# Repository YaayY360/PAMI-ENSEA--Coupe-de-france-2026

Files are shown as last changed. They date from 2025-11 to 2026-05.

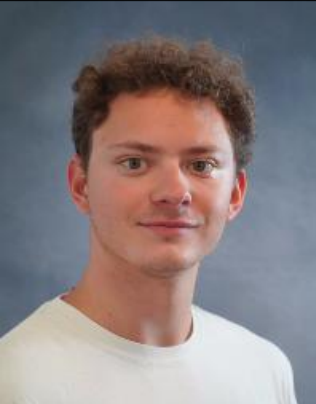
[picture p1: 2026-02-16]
Diagramme-architecture/Photo-collaborateurs/Yanis.png

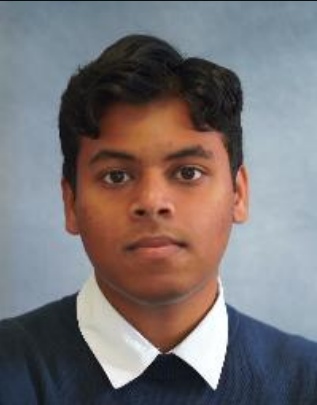
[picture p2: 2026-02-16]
Diagramme-architecture/Photo-collaborateurs/Valentin.png

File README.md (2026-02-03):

# 🔧 Coupe de france de robotique 2026 - PAMI ENSEA 

> **Objectif :** Conception et fabrication d'un robot PAMI (Petit Actionneur Motorisé Indépendant) respectant les modalités attendues pour la coupe de france de robotique 2026.
> 
> **Membres de l'équipe :**
> 
> CHERFI Iftene (1G1)
> 
> EL BAROUD Elias (1G1)
> 
> GRAVE Yanis (1G1)
> 
> LINOT Jean-Bosco (1G1)
> 
> MALEPART Alexandre (1G3)
>
> NEJJARI Mouaad (1G3)
>
> SURESHKUMAR Valentin (1G1)
---

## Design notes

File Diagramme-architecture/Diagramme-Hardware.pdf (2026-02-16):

# Diagramme d’architecture Hardware

Composant d’Alimentation | Composant Actif Microcontrôleur | Composant Passif Batterie 7.5

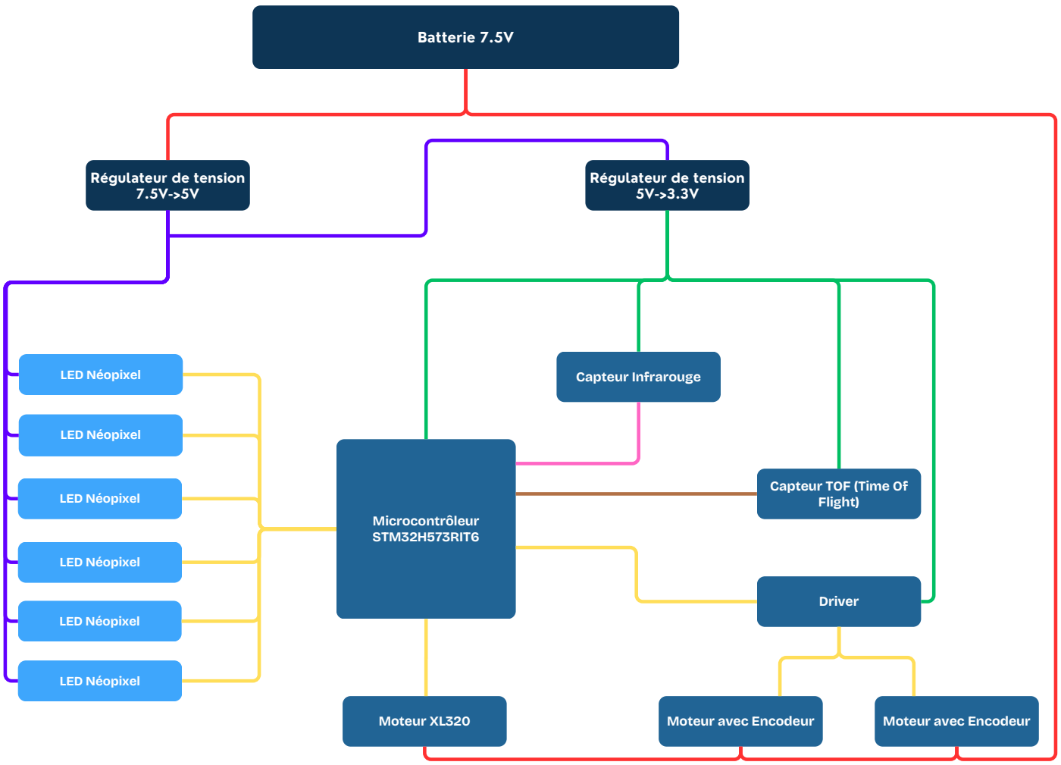
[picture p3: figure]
Régulateur de tension 7.5V->5V; Régulateur de tension 5V->3.3V; Batterie 7.5V; LED Néopixel; Capteur Infrarouge; Microcontrôleur STM32H573RIT6; Capteur TOF (Time Of Flight); Driver; Moteur XL320; Moteur avec Encodeur

| STM32H573RIT6 | LED Néopixel

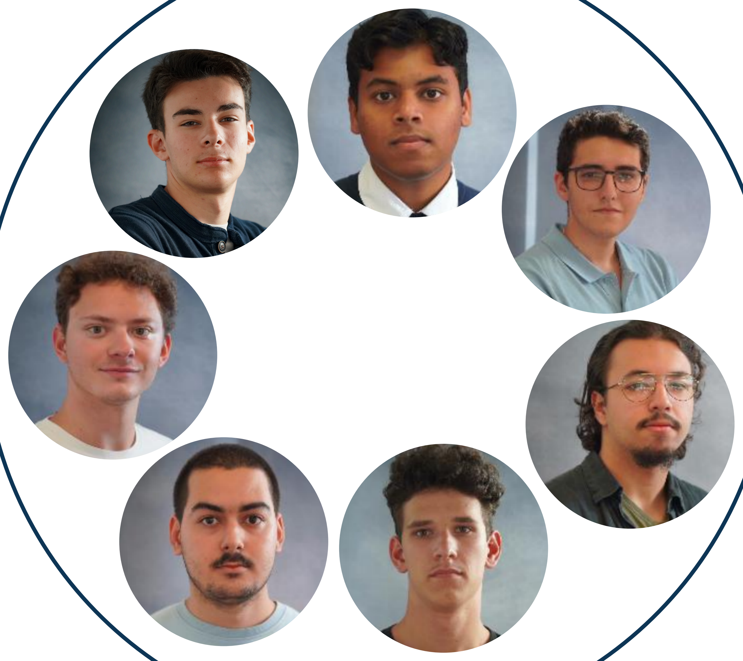
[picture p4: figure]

Régulateur de tension 7.5->5V | Capteur Infrarouge
Régulateur de tension 5->3.3V | Capteur TOF (Time Of Flight)
| Driver
| Moteur avec Encodeur
| Moteur XL320

# Colaborate

7.5V

3.3V

5V

PWM

SPI

I2C

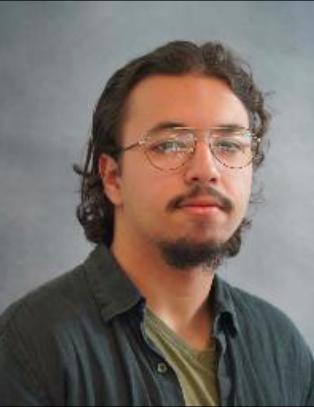
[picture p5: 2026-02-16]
Diagramme-architecture/Photo-collaborateurs/Elias.png

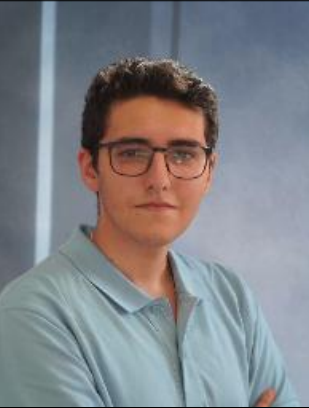
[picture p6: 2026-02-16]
Diagramme-architecture/Photo-collaborateurs/Iftene.png

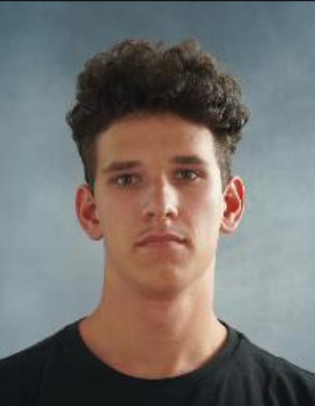
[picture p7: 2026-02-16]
Diagramme-architecture/Photo-collaborateurs/Jean.png

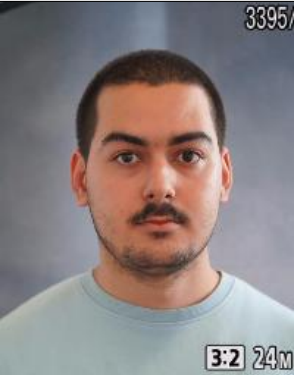
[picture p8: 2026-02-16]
Diagramme-architecture/Photo-collaborateurs/Mouaad.png

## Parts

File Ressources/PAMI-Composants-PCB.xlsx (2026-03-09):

Connecteur 01x06 pour | Référence | site fabriquant | quantité
Microcontroleur | STM32H573RIT6 |  | 1
STLINK | STLINKV3MOD |  | 1
Régulateur 3.3V | AZ1117CH2 - 3.3 |  | 1
Régulateur 5.0V | wurth elektronik DC-DC 5.0V | https://www.mouser.fr/ProductDetail/Wurth-Elektronik/173010578?qs=%252BUQ4csG8RsfFs4nK53SHEg%3D%3D | 1
Connecteurs pour 2 moteur odométriques | conn jst xh 01x06 |  | 3
Connecteur pour TOF | (horizontal) pin_header 01x06
Connecteurs
Connecteurs
Drivers pour 2 moteur odométriques | TB6612FNG |  | 1
Moteurs pour roues | Moteur CC N20-1812-EN |  | 2
Moteur pour animation | XL320 |  | 1
Led néo pixels | WS2812B RGB LED chip | https://mmwork.shop/boutique/led-adressable-ws2812b-rgb-5050-smd/
Boutons |  |  | 4
Led alim | LED CMS |  | 1
condensateur 1 MicroFarad | WCAP-CSGP Ceramic Capacitors 0603 | https://www.we-online.com/components/products/datasheet/885012206076.pdf
Capteur TOF | VL53T0

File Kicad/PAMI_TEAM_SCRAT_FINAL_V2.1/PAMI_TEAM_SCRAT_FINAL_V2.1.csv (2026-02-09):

Reference | Qty | Value | DNP | Exclude from BOM | Exclude from Board | Footprint | Datasheet
C1,C2,C3 | 3 | 10n |  |  |  | Capacitor_SMD:C_0603_1608Metric | ~
C4,C5,C6,C7,C8,C9,C10,C15,C17 | 9 | 100n |  |  |  | Capacitor_SMD:C_0603_1608Metric | ~
C11,C16,C18 | 3 | 10u |  |  |  | Capacitor_SMD:C_0603_1608Metric | ~
C12 | 1 | 22u |  |  |  | Capacitor_SMD:C_Elec_5x5.4 | ~
C13,C14 | 2 | 20p |  |  |  | Capacitor_SMD:C_0603_1608Metric | ~
C19,C20 | 2 | 22u |  |  |  | Capacitor_SMD:C_0603_1608Metric | ~
C21,C22,C23,C24,C25 | 5 | 1u |  |  |  | Capacitor_SMD:C_0603_1608Metric | ~
D1 | 1 | LED |  |  |  | LED_SMD:LED_0603_1608Metric | ~
D2,D3,D4,D5,D6,D7 | 6 | NeoPixel |  |  |  | LED_SMD:LED_WS2812B_PLCC4_5.0x5.0mm_P3.2mm | https://www.adafruit.com/product/1938
H1,H2,H3,H4 | 4 | MountingHole_Pad |  | Exclure de la Liste du Matériel |  | MountingHole:MountingHole_3.2mm_M3_DIN965_Pad | ~
J1 | 1 | ALIM |  |  |  | Connector_JST:JST_XH_B2B-XH-A_1x02_P2.50mm_Vertical | ~
J2 | 1 | TOF |  |  |  | Connector_PinSocket_2.54mm:PinSocket_1x06_P2.54mm_Horizontal | ~
J3 | 1 | IR |  |  |  | Connector_JST:JST_XH_B6B-XH-A_1x06_P2.50mm_Vertical | ~
J4 | 1 | M1 |  |  |  | Connector_JST:JST_XH_B6B-XH-A_1x06_P2.50mm_Vertical | ~
J5 | 1 | M2 |  |  |  | Connector_JST:JST_XH_B6B-XH-A_1x06_P2.50mm_Vertical | ~
J6 | 1 | XL320 |  |  |  | Connector_JST:JST_XH_B3B-XH-A_1x03_P2.50mm_Vertical | ~
R1,R2,R3,R4,R5,R6,R7 | 7 | 10k |  |  |  | Resistor_SMD:R_0603_1608Metric | ~
R8,R9 | 2 | 510 |  |  |  | Resistor_SMD:R_0603_1608Metric | ~
SW1 | 1 | BTN1 |  |  |  | Button_Switch_SMD:Panasonic_EVQPUJ_EVQPUA | ~
SW2 | 1 | BTN2 |  |  |  | Button_Switch_SMD:Panasonic_EVQPUJ_EVQPUA | ~
SW3 | 1 | BTN3 |  |  |  | Button_Switch_SMD:Panasonic_EVQPUJ_EVQPUA | ~
SW4 | 1 | RESET |  |  |  | Button_Switch_SMD:Panasonic_EVQPUJ_EVQPUA | ~
U1 | 1 | STM32H573RITx |  |  |  | Package_QFP:LQFP-64_10x10mm_P0.5mm | https://www.st.com/resource/en/datasheet/stm32h573ri.pdf
U2 | 1 | STLINK-V3MODS |  |  |  | STLINK-V3MODS:MODULE_STLINK-V3MODS
U3 | 1 | WE-DC-DC-5V |  |  |  | Converter_DCDC:Converter_DCDC_RECOM_R-78B-2.0_THT | https://www.diodes.com/assets/Datasheets/AZ1117C.pdf
U4 | 1 | AZ1117CH2-3.3 |  |  |  | Package_TO_SOT_SMD:SOT-223-3_TabPin2 | https://www.diodes.com/assets/Datasheets/AZ1117C.pdf
U5 | 1 | TB6612FNG |  |  |  | Package_SO:SSOP-24_5.3x8.2mm_P0.65mm | https://toshiba.semicon-storage.com/us/product/linear/motordriver/detail.TB6612FNG.html
Y1 | 1 | Crystal |  |  |  | Crystal:Crystal_SMD_7050-4Pin_7.0x5.0mm | ~

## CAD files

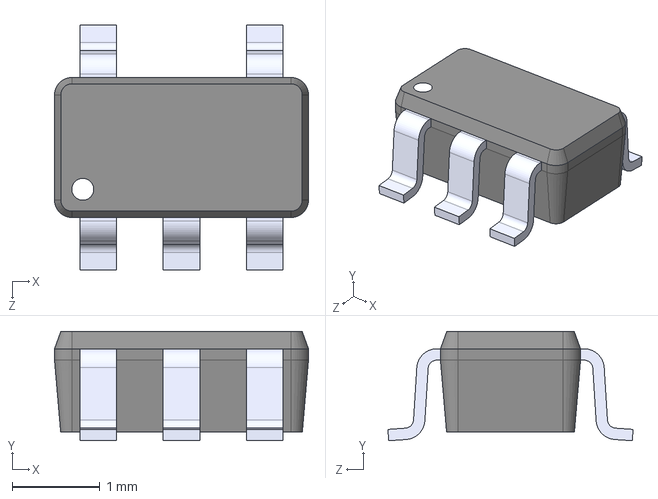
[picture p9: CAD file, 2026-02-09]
Kicad/Librairies KICAD/BU33SD5WG-TR/BU33SD5WG-TR.step
2.90 x 1.25 x 2.80 mm

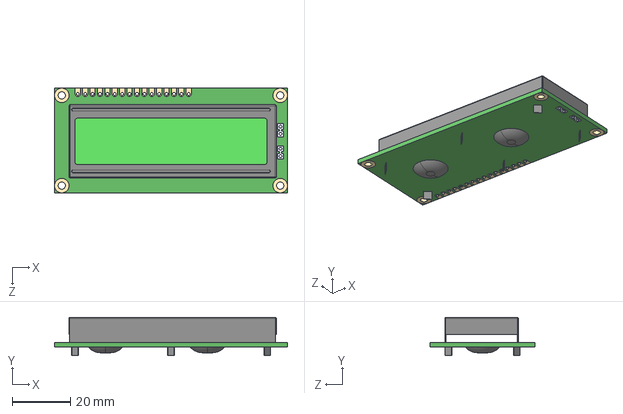
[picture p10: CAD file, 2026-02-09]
Kicad/Librairies KICAD/LCD-16X2/LCD-16X2.step
80.0 x 13.2 x 36.0 mm

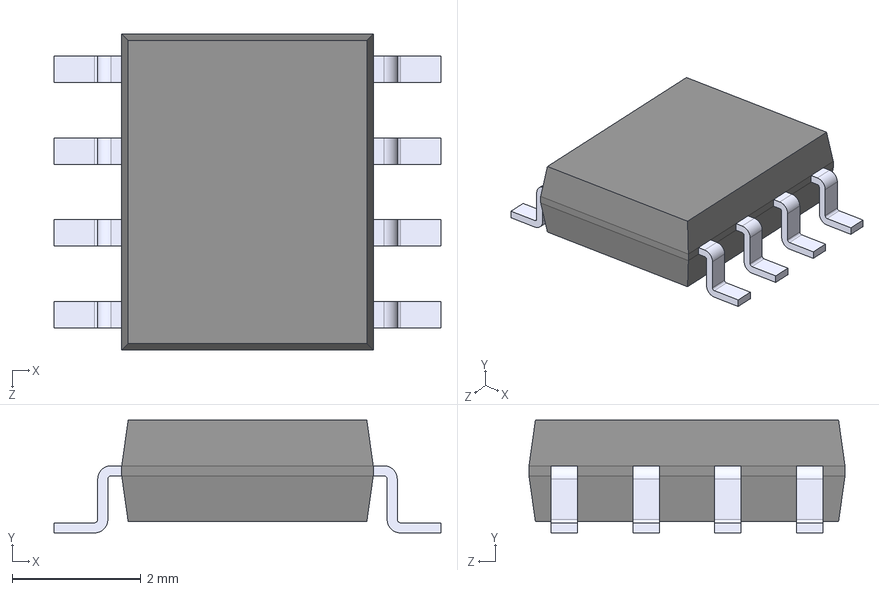
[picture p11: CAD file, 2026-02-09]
Kicad/Librairies KICAD/MCP4801-E_SN/MCP4801-E_SN.step
6.00 x 1.75 x 4.90 mm

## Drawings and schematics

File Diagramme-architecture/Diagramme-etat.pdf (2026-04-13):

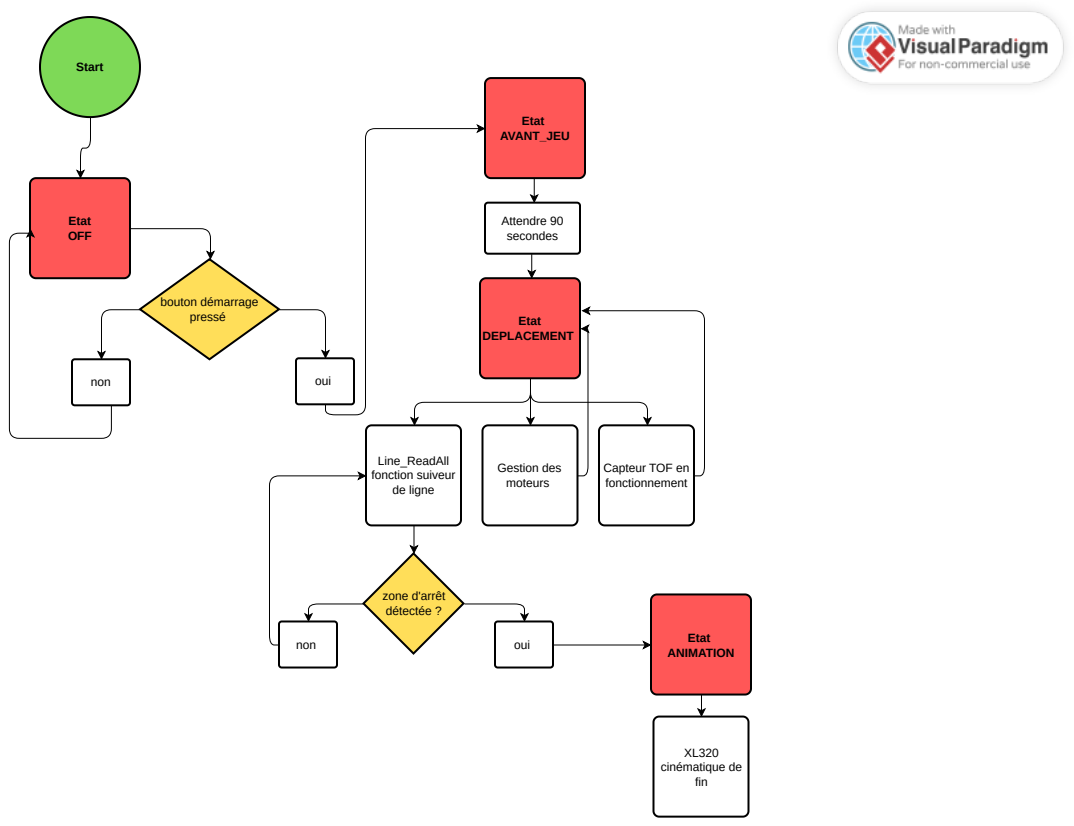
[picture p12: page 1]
Start; Etat OFF; oui; Etat AVANT_JEU; Line_ReadAll fonction suiveur de ligne; bouton démarrage pressé; non; Attendre 90 secondes; Etat DEPLACEMENT; Gestion des moteurs; zone d'arrêt détectée ?; Etat; ANIMATION; XL320 cinématique de fin

Capteur TOF en
fonctionnement

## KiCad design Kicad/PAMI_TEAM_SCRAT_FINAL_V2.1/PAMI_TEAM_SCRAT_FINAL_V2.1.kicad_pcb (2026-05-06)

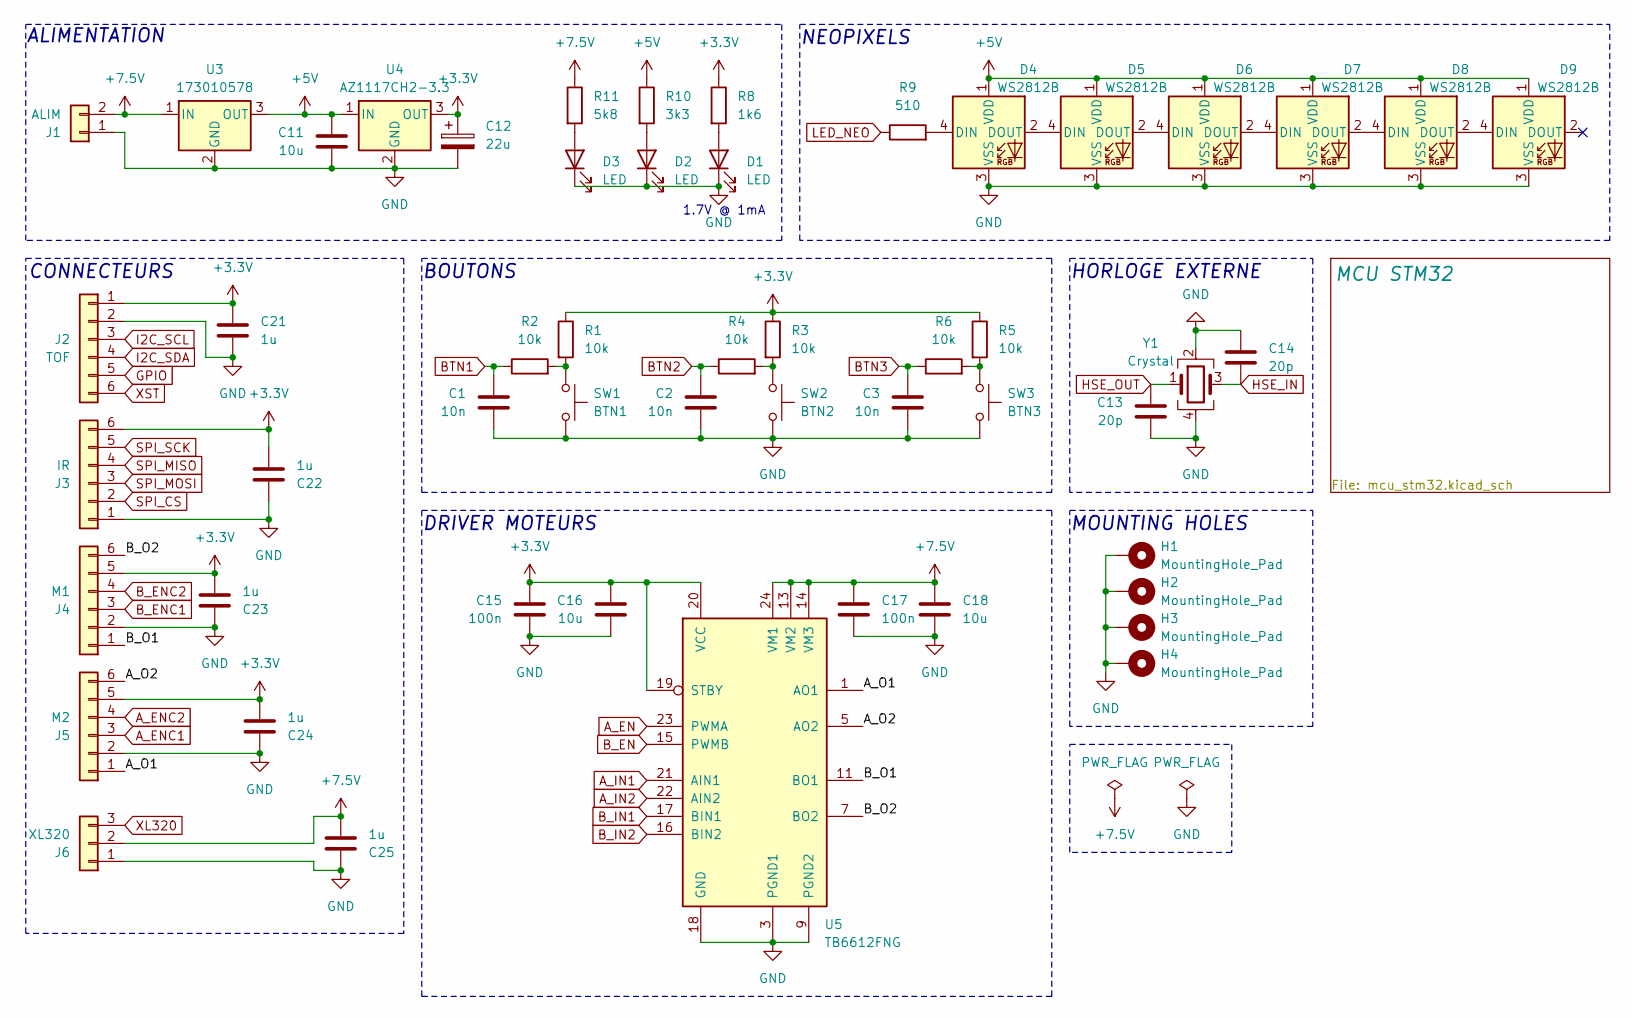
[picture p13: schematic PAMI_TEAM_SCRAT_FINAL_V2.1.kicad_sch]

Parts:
C1, C2, C3: 10n; C_0603_1608Metric
C11, C16, C18: 10u; C_0603_1608Metric
C12: 22u; CP_Elec_5x5.4
C13, C14: 20p; C_0603_1608Metric
C15, C17: 100n; C_0603_1608Metric
C21, C22, C23, C24, C25: 1u; C_0603_1608Metric
D1, D2, D3: LED; LED_0603_1608Metric; MPN 150060RS55040
D4, D5, D6, D7, D8, D9: WS2812B; LED_WS2812B_PLCC4_5.0x5.0mm_P3.2mm
H1, H2, H3, H4: MountingHole_Pad; MountingHole_3.2mm_M3_DIN965_Pad
J1: ALIM; JST_XH_B2B-XH-A_1x02_P2.50mm_Vertical
J2: TOF; PinSocket_1x06_P2.54mm_Horizontal
J3: IR; JST_XH_B6B-XH-A_1x06_P2.50mm_Vertical
J4: M1; JST_XH_B6B-XH-A_1x06_P2.50mm_Vertical
J5: M2; JST_XH_B6B-XH-A_1x06_P2.50mm_Vertical
J6: XL320; JST_XH_B3B-XH-A_1x03_P2.50mm_Vertical
R1, R2, R3, R4, R5, R6: 10k; R_0603_1608Metric
R8: 1k6; R_0603_1608Metric
R9: 510; R_0603_1608Metric
R10: 3k3; R_0603_1608Metric
R11: 5k8; R_0603_1608Metric
SW1: BTN1; SW_SPST_PTS645Sx43SMTR92
SW2: BTN2; SW_SPST_PTS645Sx43SMTR92
SW3: BTN3; SW_SPST_PTS645Sx43SMTR92
U3: 173010578; Converter_DCDC_RECOM_R-78E-0.5_THT; MPN 173010578
U4: AZ1117CH2-3.3; SOT-223-3_TabPin2
U5: TB6612FNG; SSOP-24_5.3x8.2mm_P0.65mm
Y1: Crystal; Crystal_SMD_7050-4Pin_7.0x5.0mm

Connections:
+3.3V: C12.1, C15.1, C16.1, C21.1, C22.2, C23.2, C24.2, J2.1, J3.6, J4.5, J5.5, R1.1, R3.1, R5.1, R8.1, U4.3 (OUT), U5.19 (STBY), U5.20 (VCC); also elsewhere on the board
+5V: C11.1, D4.1 (VDD), D5.1 (VDD), D6.1 (VDD), D7.1 (VDD), D8.1 (VDD), D9.1 (VDD), R10.1, U3.3 (OUT), U4.1 (IN)
+7.5V: C17.1, C18.1, C25.2, J1.2, J6.2, R11.1, U3.1 (IN), U5.13 (VM2), U5.14 (VM3), U5.24 (VM1)
/A_O1: J5.1, U5.1 (AO1), U5.2 (AO1)
/A_O2: J5.6, U5.5 (AO2), U5.6 (AO2)
/B_O1: J4.1, U5.11 (BO1), U5.12 (BO1)
/B_O2: J4.6, U5.7 (BO2), U5.8 (BO2)
A_EN: U5.23 (PWMA); also elsewhere on the board
A_ENC1: J5.3; also elsewhere on the board
A_ENC2: J5.4; also elsewhere on the board
A_IN1: U5.21 (AIN1); also elsewhere on the board
A_IN2: U5.22 (AIN2); also elsewhere on the board
BTN1: C1.1, R2.1; also elsewhere on the board
BTN2: C2.1, R4.1; also elsewhere on the board
BTN3: C3.1, R6.1; also elsewhere on the board
B_EN: U5.15 (PWMB); also elsewhere on the board
B_ENC1: J4.3; also elsewhere on the board
B_ENC2: J4.4; also elsewhere on the board
B_IN1: U5.17 (BIN1); also elsewhere on the board
B_IN2: U5.16 (BIN2); also elsewhere on the board
GND: C1.2, C2.2, C3.2, C11.2, C12.2, C13.2, C14.1, C15.2, C16.2, C17.2, C18.2, C21.2, C22.1, C23.1, C24.1, C25.1, D1.1 (K), D2.1 (K), D3.1 (K), D4.3 (VSS), D5.3 (VSS), D6.3 (VSS), D7.3 (VSS), D8.3 (VSS), D9.3 (VSS), H1.1, H2.1, H3.1, H4.1, J1.1, J2.2, J3.1, J4.2, J5.2, J6.1, SW1.2, SW2.2, SW3.2, U3.2 (GND), U4.2 (GND), U5.3 (PGND1), U5.4 (PGND1), U5.9 (PGND2), U5.10 (PGND2), U5.18 (GND), Y1.2, Y1.4; also elsewhere on the board
GPIO: J2.5; also elsewhere on the board
HSE_IN: C14.2, Y1.3; also elsewhere on the board
HSE_OUT: C13.1, Y1.1; also elsewhere on the board
I2C_SCL: J2.3; also elsewhere on the board
I2C_SDA: J2.4; also elsewhere on the board
LED_NEO: R9.1; also elsewhere on the board
unnamed: D1.2 (A), R8.2
unnamed: D2.2 (A), R10.2
unnamed: D3.2 (A), R11.2
unnamed: D4.4 (DIN), R9.2
unnamed: D4.2 (DOUT), D5.4 (DIN)
unnamed: D5.2 (DOUT), D6.4 (DIN)
unnamed: D6.2 (DOUT), D7.4 (DIN)
unnamed: D7.2 (DOUT), D8.4 (DIN)
unnamed: D8.2 (DOUT), D9.4 (DIN)
unnamed: R1.2, R2.2, SW1.1
unnamed: R3.2, R4.2, SW2.1
unnamed: R5.2, R6.2, SW3.1
SPI_CS: J3.2; also elsewhere on the board
SPI_MISO: J3.4; also elsewhere on the board
SPI_MOSI: J3.3; also elsewhere on the board
SPI_SCK: J3.5; also elsewhere on the board
XL320: J6.3; also elsewhere on the board
XST: J2.6; also elsewhere on the board

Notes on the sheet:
CONNECTEURS
MOUNTING HOLES
BOUTONS
NEOPIXELS
HORLOGE EXTERNE
DRIVER MOTEURS
ALIMENTATION
1.7V @ 1mA

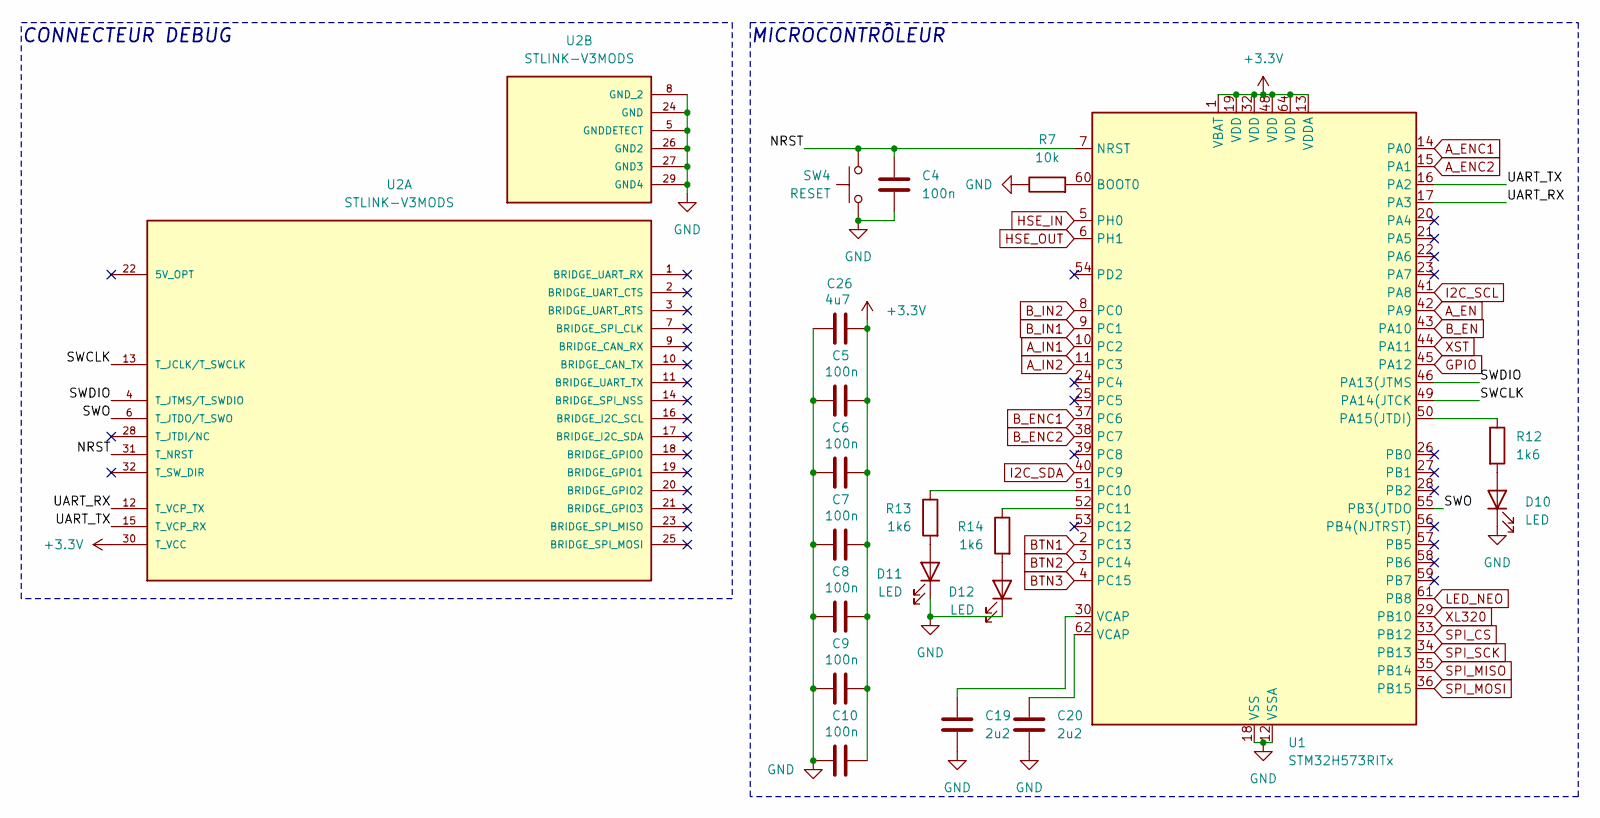
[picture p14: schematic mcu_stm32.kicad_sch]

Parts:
C4, C5, C6, C7, C8, C9, C10: 100n; C_0603_1608Metric
C19, C20: 2u2; C_0603_1608Metric
C26: 4u7; C_0603_1608Metric
D10, D11, D12: LED; LED_0603_1608Metric; MPN 150060RS55040
R7: 10k; R_0603_1608Metric
R12, R13, R14: 1k6; R_0603_1608Metric
SW4: RESET; SW_SPST_PTS645Sx43SMTR92
U1: STM32H573RITx; LQFP-64_10x10mm_P0.5mm
U2: STLINK-V3MODS; MODULE_STLINK-V3MODS; PARTREV 1

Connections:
+3.3V: C5.2, C6.2, C7.2, C8.2, C9.2, C10.2, C26.2, U1.1 (VBAT), U1.13 (VDDA), U1.19 (VDD), U1.32 (VDD), U1.48 (VDD), U1.64 (VDD), U2.30 (T_VCC); also elsewhere on the board
/MCU STM32/NRST: C4.1, SW4.1, U1.7 (NRST), U2.31 (T_NRST)
/MCU STM32/SWCLK: U1.49 (PA14(JTCK), U2.13 (T_JCLK/T_SWCLK)
/MCU STM32/SWDIO: U1.46 (PA13(JTMS), U2.4 (T_JTMS/T_SWDIO)
/MCU STM32/SWO: U1.55 (PB3(JTDO), U2.6 (T_JTDO/T_SWO)
/MCU STM32/UART_RX: U1.17 (PA3), U2.12 (T_VCP_TX)
/MCU STM32/UART_TX: U1.16 (PA2), U2.15 (T_VCP_RX)
A_EN: U1.42 (PA9); also elsewhere on the board
A_ENC1: U1.14 (PA0); also elsewhere on the board
A_ENC2: U1.15 (PA1); also elsewhere on the board
A_IN1: U1.10 (PC2); also elsewhere on the board
A_IN2: U1.11 (PC3); also elsewhere on the board
BTN1: U1.2 (PC13); also elsewhere on the board
BTN2: U1.3 (PC14); also elsewhere on the board
BTN3: U1.4 (PC15); also elsewhere on the board
B_EN: U1.43 (PA10); also elsewhere on the board
B_ENC1: U1.37 (PC6); also elsewhere on the board
B_ENC2: U1.38 (PC7); also elsewhere on the board
B_IN1: U1.9 (PC1); also elsewhere on the board
B_IN2: U1.8 (PC0); also elsewhere on the board
GND: C4.2, C5.1, C6.1, C7.1, C8.1, C9.1, C10.1, C19.2, C20.2, C26.1, D10.1 (K), D11.1 (K), D12.1 (K), R7.1, SW4.2, U1.12 (VSSA), U1.18 (VSS), U1.31 (VSS), U1.47 (VSS), U1.63 (VSS), U2.5 (GNDDETECT), U2.8 (GND_2), U2.24 (GND), U2.26 (GND2), U2.27 (GND3), U2.29 (GND4); also elsewhere on the board
GPIO: U1.45 (PA12); also elsewhere on the board
HSE_IN: U1.5 (PH0); also elsewhere on the board
HSE_OUT: U1.6 (PH1); also elsewhere on the board
I2C_SCL: U1.41 (PA8); also elsewhere on the board
I2C_SDA: U1.40 (PC9); also elsewhere on the board
LED_NEO: U1.61 (PB8); also elsewhere on the board
unnamed: C19.1, U1.30 (VCAP)
unnamed: C20.1, U1.62 (VCAP)
unnamed: D10.2 (A), R12.2
unnamed: D11.2 (A), R13.2
unnamed: D12.2 (A), R14.2
unnamed: R7.2, U1.60 (BOOT0)
unnamed: R12.1, U1.50 (PA15(JTDI))
unnamed: R13.1, U1.51 (PC10)
unnamed: R14.1, U1.52 (PC11)
SPI_CS: U1.33 (PB12); also elsewhere on the board
SPI_MISO: U1.35 (PB14); also elsewhere on the board
SPI_MOSI: U1.36 (PB15); also elsewhere on the board
SPI_SCK: U1.34 (PB13); also elsewhere on the board
XL320: U1.29 (PB10); also elsewhere on the board
XST: U1.44 (PA11); also elsewhere on the board

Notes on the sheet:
CONNECTEUR DEBUG
MICROCONTRÔLEUR

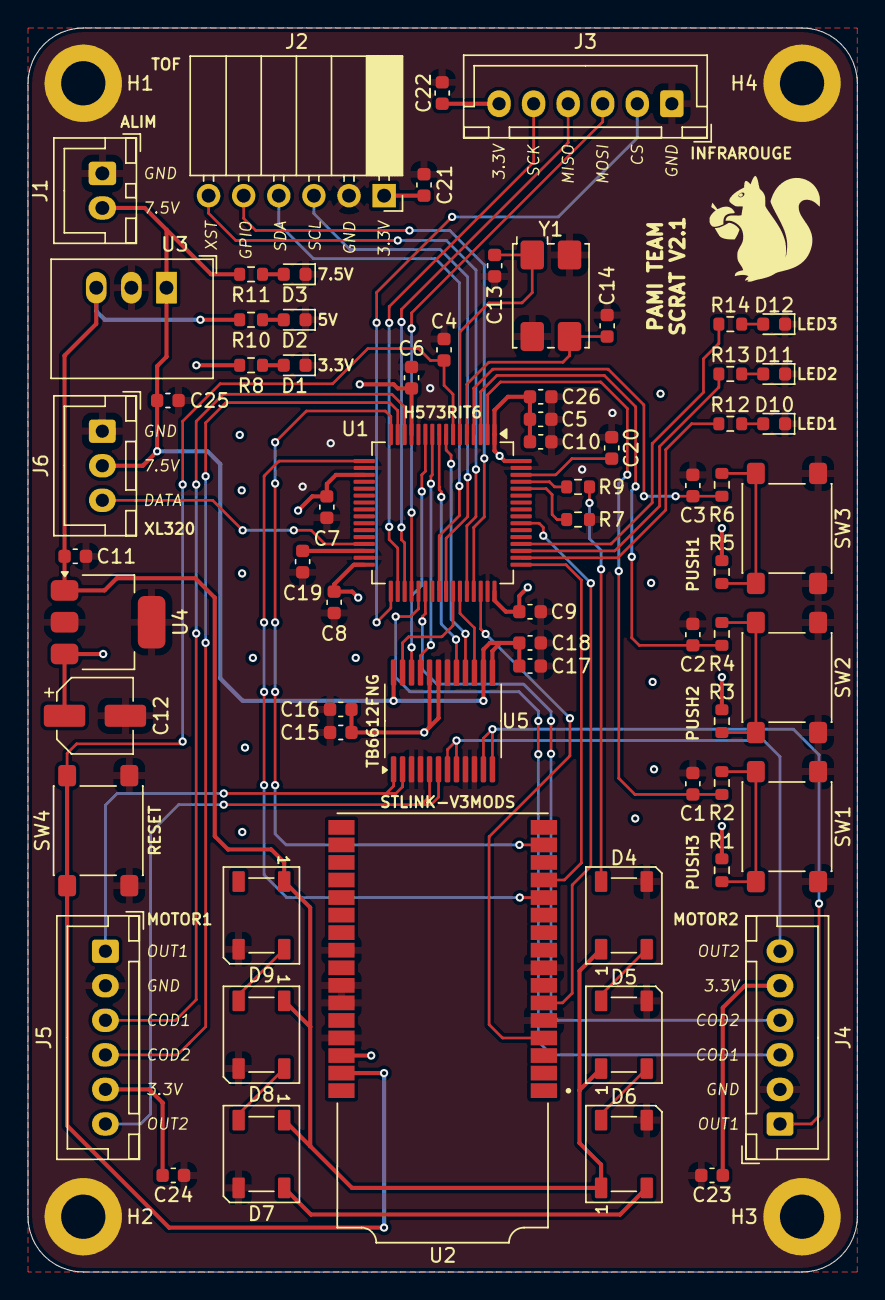
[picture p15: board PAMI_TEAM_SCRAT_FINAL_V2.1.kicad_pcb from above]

Board: 4 copper layers, 60.0 x 90.0 mm, 72 parts (0 on the bottom side), 60 nets.

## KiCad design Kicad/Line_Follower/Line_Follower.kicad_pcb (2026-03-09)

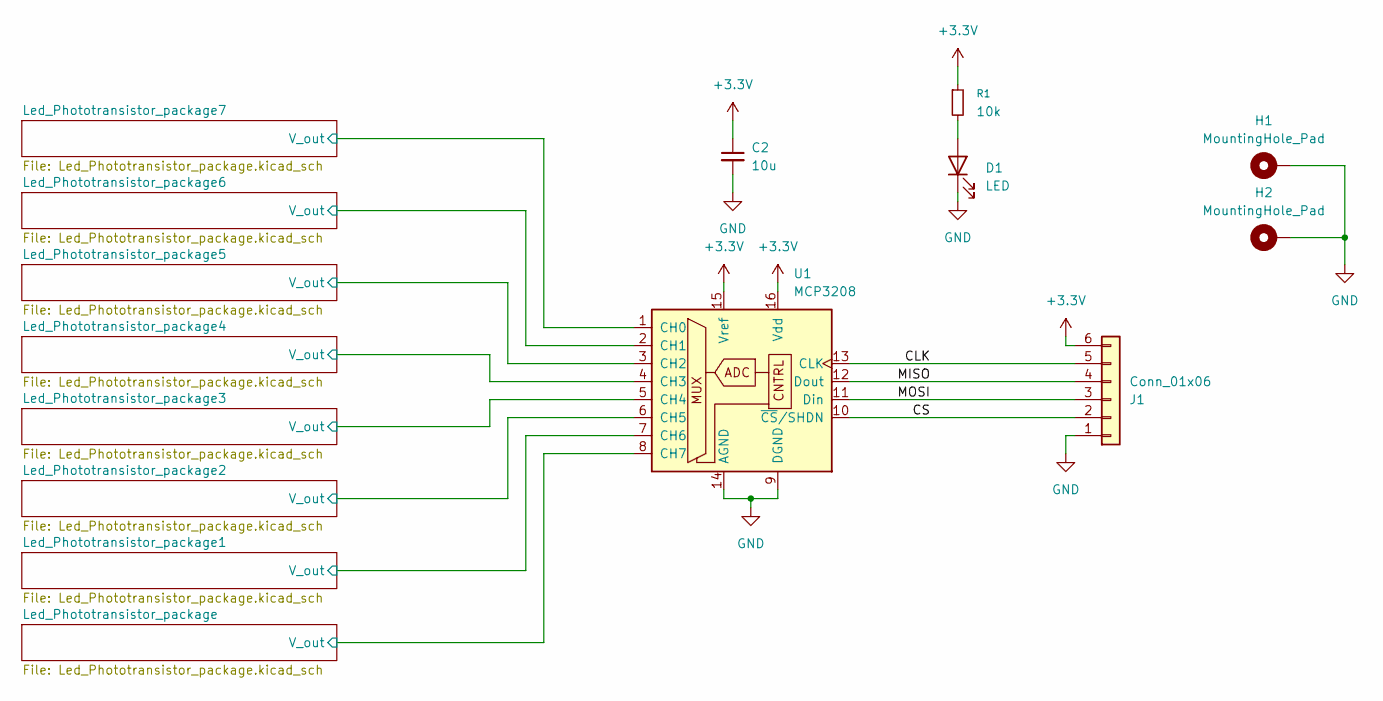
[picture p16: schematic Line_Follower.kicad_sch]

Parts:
C2: 10u; C_0603_1608Metric
D1: LED
H1, H2: MountingHole_Pad
J1: Conn_01x06
R1: 10k
U1: MCP3208

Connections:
+3.3V: C2.1, J1.6, R1.1, U1.15 (Vref), U1.16 (Vdd); also elsewhere on the board
/CLK: J1.5, U1.13 (CLK)
/CS: J1.2, U1.10 (~CS/SHDN)
/Led_Phototransistor_package1/V_out: U1.7 (CH6); also elsewhere on the board
/Led_Phototransistor_package2/V_out: U1.6 (CH5); also elsewhere on the board
/Led_Phototransistor_package3/V_out: U1.5 (CH4); also elsewhere on the board
/Led_Phototransistor_package4/V_out: U1.4 (CH3); also elsewhere on the board
/Led_Phototransistor_package5/V_out: U1.3 (CH2); also elsewhere on the board
/Led_Phototransistor_package6/V_out: U1.2 (CH1); also elsewhere on the board
/Led_Phototransistor_package7/V_out: U1.1 (CH0); also elsewhere on the board
/Led_Phototransistor_package/V_out: U1.8 (CH7); also elsewhere on the board
/MISO: J1.4, U1.12 (Dout)
/MOSI: J1.3, U1.11 (Din)
GND: C2.2, D1.1 (K), H1.1, H2.1, J1.1, U1.9 (DGND), U1.14 (AGND); also elsewhere on the board
unnamed: D1.2 (A), R1.2

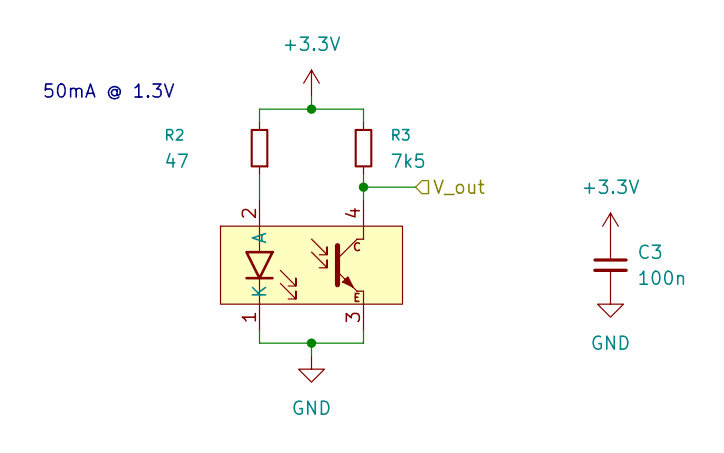
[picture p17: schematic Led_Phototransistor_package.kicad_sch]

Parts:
C3: 100n; C_0603_1608Metric
R2: 47
R3: 7k5
U2: (no value)

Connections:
+3.3V: C3.1, R2.2, R3.1; also elsewhere on the board
/Led_Phototransistor_package/V_out: R3.2, U2.4; also elsewhere on the board
GND: C3.2, U2.1 (K), U2.3; also elsewhere on the board
unnamed: R2.1, U2.2 (A)

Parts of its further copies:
C4, C5, C6, C7, C8, C9, C10: 100n; C_0603_1608Metric
R4, R6, R8, R10, R12, R14, R16: 47
R5, R7, R9, R11, R13, R15, R17: 7k5
U3, U4, U5, U6, U7, U8, U9: (no value)

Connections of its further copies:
+3.3V: C4.1, C5.1, C6.1, C7.1, C8.1, C9.1, C10.1, R4.2, R5.1, R6.2, R7.1, R8.2, R9.1, R10.2, R11.1, R12.2, R13.1, R14.2, R15.1, R16.2, R17.1; also elsewhere on the board
/Led_Phototransistor_package1/V_out: R5.2, U3.4; also elsewhere on the board
/Led_Phototransistor_package2/V_out: R7.2, U4.4; also elsewhere on the board
/Led_Phototransistor_package3/V_out: R9.2, U5.4; also elsewhere on the board
/Led_Phototransistor_package4/V_out: R11.2, U6.4; also elsewhere on the board
/Led_Phototransistor_package5/V_out: R13.2, U7.4; also elsewhere on the board
/Led_Phototransistor_package6/V_out: R15.2, U8.4; also elsewhere on the board
/Led_Phototransistor_package7/V_out: R17.2, U9.4; also elsewhere on the board
GND: C4.2, C5.2, C6.2, C7.2, C8.2, C9.2, C10.2, U3.1 (K), U3.3, U4.1 (K), U4.3, U5.1 (K), U5.3, U6.1 (K), U6.3, U7.1 (K), U7.3, U8.1 (K), U8.3, U9.1 (K), U9.3; also elsewhere on the board
unnamed: R4.1, U3.2 (A)
unnamed: R6.1, U4.2 (A)
unnamed: R8.1, U5.2 (A)
unnamed: R10.1, U6.2 (A)
unnamed: R12.1, U7.2 (A)
unnamed: R14.1, U8.2 (A)
unnamed: R16.1, U9.2 (A)

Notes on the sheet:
50mA @ 1.3V

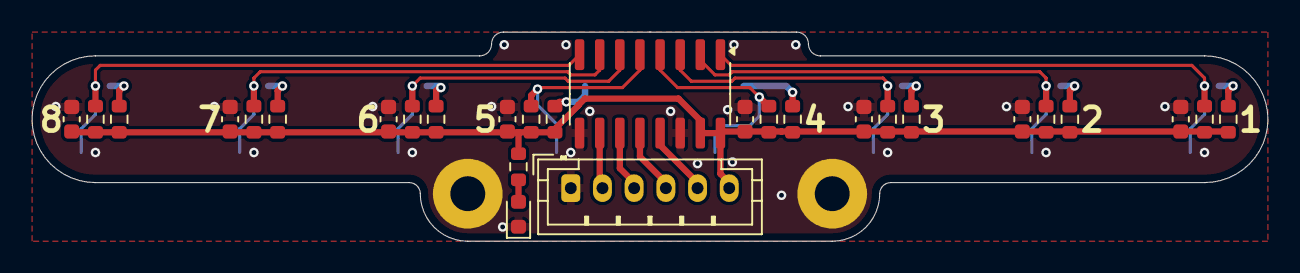
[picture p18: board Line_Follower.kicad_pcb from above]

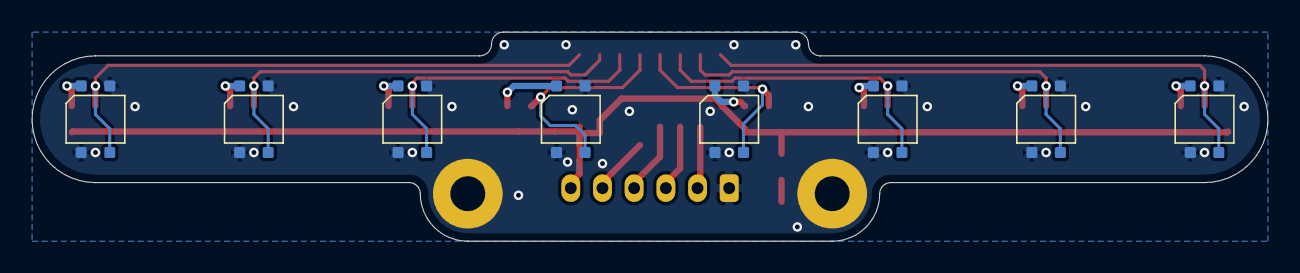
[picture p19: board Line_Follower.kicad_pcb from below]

Board: 2 copper layers, 78.0 x 13.2 mm, 38 parts (8 on the bottom side), 23 nets.

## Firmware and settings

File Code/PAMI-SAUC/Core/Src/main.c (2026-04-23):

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
/* Includes ------------------------------------------------------------------*/
#include "main.h"

/* USER CODE BEGIN Includes */
#include "utils.h"
/* USER CODE END Includes */

/* USER CODE BEGIN PTD */
enum etat_jeu { OFF, AVANT_JEU, DEPLACEMENT, ANIMATION };
/* USER CODE END PTD */


I2C_HandleTypeDef hi2c3;

SPI_HandleTypeDef hspi2;

TIM_HandleTypeDef htim1;
TIM_HandleTypeDef htim2;
TIM_HandleTypeDef htim3;
TIM_HandleTypeDef htim4;
TIM_HandleTypeDef htim8;

UART_HandleTypeDef huart2;

/* USER CODE BEGIN PV */
enum etat_jeu etape = OFF;
statInfo_t_VL53L0X distanceStr;
LineSensor_t lineFollower;
uint8_t detection_IR;
uint16_t distance;
bool M1 = 1, M2 = 1;
/* USER CODE END PV */

void SystemClock_Config(void);
static void MX_GPIO_Init(void);
static void MX_I2C3_Init(void);
static void MX_SPI2_Init(void);
static void MX_TIM1_Init(void);
static void MX_TIM2_Init(void);
static void MX_TIM3_Init(void);
static void MX_TIM4_Init(void);
static void MX_TIM8_Init(void);
static void MX_USART2_UART_Init(void);
static void MX_ICACHE_Init(void);
/* USER CODE BEGIN 0 */
int __io_putchar(int ch)
{
	HAL_UART_Transmit(&huart2, (uint8_t *)&ch, 1, HAL_MAX_DELAY);
	return ch;
}

int __io_getchar(void)
{
	uint8_t ch = 0;
	__HAL_UART_CLEAR_OREFLAG(&huart2);
	HAL_UART_Receive(&huart2, (uint8_t *)&ch, 1, HAL_MAX_DELAY);
	HAL_UART_Transmit(&huart2, (uint8_t *)&ch, 1, HAL_MAX_DELAY);
	return ch;
}
/* USER CODE END 0 */

/**
  * @brief  The application entry point.
  * @retval int
  */
int main(void)
{

  /* USER CODE BEGIN 1 */
  Line_Init(&lineFollower, &hspi2, SPI2_CS_GPIO_Port, SPI2_CS_Pin, 8);
  //initVL53L0X(1, &hi2c3);
  printf("Calibration Capteurs Ligne (0-4095)\r\n");

  /* USER CODE END 1 */

  /* MCU Configuration--------------------------------------------------------*/

  /* Reset of all peripherals, Initializes the Flash interface and the Systick. */
  HAL_Init();

  /* Configure the system clock */
  SystemClock_Config();

  /* Initialize all configured peripherals */
  MX_GPIO_Init();
  MX_I2C3_Init();
  MX_SPI2_Init();
  MX_TIM1_Init();
  MX_TIM2_Init();
  MX_TIM3_Init();
  MX_TIM4_Init();
  MX_TIM8_Init();
  MX_USART2_UART_Init();
  MX_ICACHE_Init();
  /* USER CODE BEGIN 2 */
  HAL_TIM_PWM_Start(&htim1, TIM_CHANNEL_2); HAL_TIM_PWM_Start(&htim1, TIM_CHANNEL_3);
  HAL_GPIO_WritePin(GPIOC, A_IN1_Pin, 1); HAL_GPIO_WritePin(GPIOC, A_IN2_Pin, 0);
  HAL_GPIO_WritePin(GPIOC, B_IN1_Pin, 1); HAL_GPIO_WritePin(GPIOC, B_IN2_Pin, 0);
	setSignalRateLimit(200);
	setVcselPulsePeriod(VcselPeriodPreRange, 10);
	setVcselPulsePeriod(VcselPeriodFinalRange, 14);
	//setMeasurementTimingBudget(300 * 1000UL);
  /* USER CODE END 2 */

  /* Infinite loop */
  /* USER CODE BEGIN WHILE */
  while (1)
  {
	  /*int test=0;
	  HAL_GPIO_ReadPin(BTN1_GPIO_Port , BTN1_Pin);
	  test=HAL_GPIO_ReadPin(BTN1_GPIO_Port , BTN1_Pin);
	  */

	  /*switch(etape)
	  {
	  case OFF :
		  break;
	  case AVANT_JEU :
		  HAL_Delay(90000);
		  etape++;
		  break;
	  case DEPLACEMENT :
		  Line_ReadAll(&lineFollower);
		  distance = readRangeSingleMillimeters(&distanceStr);
		  printf("C1:%d C2:%d C3:%d C4:%d C5:%d C6:%d C7:%d C8:%d\r\n",
		         lineFollower.sensorValues[1], lineFollower.sensorValues[2],
		         lineFollower.sensorValues[3], lineFollower.sensorValues[4],
		         lineFollower.sensorValues[5], lineFollower.sensorValues[6],
		         lineFollower.sensorValues[7], lineFollower.sensorValues[0]);
		  for(int i=0; i<8; i++)
			  if(lineFollower.sensorValues[i]>3000) lineFollower.sensorValues[i] = 1;
			  else                                  lineFollower.sensorValues[i] = 0;
		  detection_IR = (lineFollower.sensorValues[1] << 7) | (lineFollower.sensorValues[2] << 6) |
				         (lineFollower.sensorValues[3] << 5) | (lineFollower.sensorValues[4] << 4) |
				         (lineFollower.sensorValues[5] << 3) | (lineFollower.sensorValues[6] << 2) |
				         (lineFollower.sensorValues[7] << 1) | (lineFollower.sensorValues[0] << 0) ;
		  switch(detection_IR)
		  {
		  case 0b00011000 :
			  M1 = M2 = 1;
			  break;
		  case 0b00000000 :
			  M1 = M2 = 0;
			  break;
		  case 0b00001000 :
			  M1 = 1; M2 = 0;
			  break;
		  case 0b00010000 :
			  M1 = 0; M2 = 1;
			  break;
		  }
		  Moteurs(M1,M2);
		  if(distance < 10) { M1 = M2 = 0; }
		  break;
	  case ANIMATION :
		  // Fonction pour effectuer le salut avec le XL320
		  etape--;
		  break;
	  }*/
    /* USER CODE END WHILE */

    /* USER CODE BEGIN 3 */
  }
  /* USER CODE END 3 */
}

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
/* USER CODE BEGIN 4 */
/*void HAL_GPIO_EXTI_Callback(uint16_t GPIO_Pin)
{
	switch(GPIO_Pin)
	{
	case BTN1_Pin :
		//if(etape == OFF) { etape++; HAL_GPIO_WritePin(LED1_GPIO_Port, LED1_Pin, 1); }
		HAL_GPIO_TogglePin(LED1_GPIO_Port, LED1_Pin);
		break;
	case BTN2_Pin :
		//
		HAL_GPIO_TogglePin(LED2_GPIO_Port, LED2_Pin);
		break;
	case BTN3_Pin :
		//
		HAL_GPIO_TogglePin(LED3_GPIO_Port, LED3_Pin);
		break;
	}
}*/
/* USER CODE END 4 */
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


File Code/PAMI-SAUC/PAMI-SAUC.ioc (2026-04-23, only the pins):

Mcu.UserName=STM32H573RITx
PA0.Signal=S_TIM2_CH1
PA1.Signal=S_TIM2_CH2
PA10.Signal=S_TIM1_CH3
PA11.GPIO_Label=XST
PA11.Signal=GPIO_Output
PA12.GPIO_Label=GPIO1
PA12.Signal=GPIO_Input
PA13(JTMS/SWDIO).Signal=DEBUG_JTMS-SWDIO
PA14(JTCK/SWCLK).Signal=DEBUG_JTCK-SWCLK
PA15(JTDI).GPIO_Label=LED1
PA15(JTDI).Signal=GPIO_Output
PA2.Signal=USART2_TX
PA3.Signal=USART2_RX
PA8.Signal=I2C3_SCL
PA9.Signal=S_TIM1_CH2
PB12.GPIO_Label=SPI2_CS
PB12.Signal=GPIO_Output
PB13.Signal=SPI2_SCK
PB14.Signal=SPI2_MISO
PB15.Signal=SPI2_MOSI
PB3(JTDO/TRACESWO).Signal=DEBUG_JTDO-SWO
PB8.Signal=S_TIM4_CH3
PC0.GPIO_Label=B_IN2
PC0.Signal=GPIO_Output
PC1.GPIO_Label=B_IN1
PC1.Signal=GPIO_Output
PC10.GPIO_Label=LED2
PC10.Signal=GPIO_Output
PC11.GPIO_Label=LED3
PC11.Signal=GPIO_Output
PC13.GPIO_Label=BTN1
PC13.Signal=GPXTI13
PC14-OSC32_IN(OSC32_IN).GPIO_Label=BTN2
PC14-OSC32_IN(OSC32_IN).Signal=GPXTI14
PC15-OSC32_OUT(OSC32_OUT).GPIO_Label=BTN3
PC15-OSC32_OUT(OSC32_OUT).Signal=GPXTI15
PC2.GPIO_Label=A_IN1
PC2.Signal=GPIO_Output
PC3.GPIO_Label=A_IN2
PC3.Signal=GPIO_Output
PC6.Signal=S_TIM3_CH1
PC7.Signal=S_TIM3_CH2
PC8.Signal=S_TIM8_CH3
PC9.Signal=I2C3_SDA
PH0-OSC_IN(PH0).Signal=RCC_OSC_IN
PH1-OSC_OUT(PH1).Signal=RCC_OSC_OUT

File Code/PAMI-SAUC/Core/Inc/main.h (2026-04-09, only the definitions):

#define BTN1_Pin GPIO_PIN_13
#define BTN1_GPIO_Port GPIOC
#define BTN1_EXTI_IRQn EXTI13_IRQn
#define BTN2_Pin GPIO_PIN_14
#define BTN2_GPIO_Port GPIOC
#define BTN2_EXTI_IRQn EXTI14_IRQn
#define BTN3_Pin GPIO_PIN_15
#define BTN3_GPIO_Port GPIOC
#define BTN3_EXTI_IRQn EXTI15_IRQn
#define B_IN2_Pin GPIO_PIN_0
#define B_IN2_GPIO_Port GPIOC
#define B_IN1_Pin GPIO_PIN_1
#define B_IN1_GPIO_Port GPIOC
#define A_IN1_Pin GPIO_PIN_2
#define A_IN1_GPIO_Port GPIOC
#define A_IN2_Pin GPIO_PIN_3
#define A_IN2_GPIO_Port GPIOC
#define SPI2_CS_Pin GPIO_PIN_12
#define SPI2_CS_GPIO_Port GPIOB
#define XST_Pin GPIO_PIN_11
#define XST_GPIO_Port GPIOA
#define GPIO1_Pin GPIO_PIN_12
#define GPIO1_GPIO_Port GPIOA
#define LED1_Pin GPIO_PIN_15
#define LED1_GPIO_Port GPIOA
#define LED2_Pin GPIO_PIN_10
#define LED2_GPIO_Port GPIOC
#define LED3_Pin GPIO_PIN_11
#define LED3_GPIO_Port GPIOC

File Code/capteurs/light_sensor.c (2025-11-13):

#include <light_sensor.h>

bool LS, CLS, CRS, RS;

void setup() {
	//
}

void loop() {

	// ATTRIBUTION DES CAPTEURS A LEUR VARIABLES

	LS= HAL_GPIO_ReadPin(GPIOA, GPIO_PIN_9); // left_sensor
	CLS= HAL_GPIO_ReadPin(GPIOA, GPIO_PIN_8); // central_left_censor
	CRS= HAL_GPIO_ReadPin(GPIOA, GPIO_PIN_7); // central_right_sensor
	RS= HAL_GPIO_ReadPin(GPIOA, GPIO_PIN_6); // right_sensor

	// TEST AVEC PRINTF
	if(CLS && CRS)
		printf("The system is centered\r\n");
	else if(!CLS && !CRS)
		printf("The system is out of track\r\n");
	else if(!CRS)
		printf("The system must go left to remain on track\r\n");
	else if(!CLS)
		printf("The system must go right to remain on track\r\n");
}

// Réalisé en collaboration avec gotaga (coco)

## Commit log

2025-10-23 Update line follower sensor contributors in README
2025-10-26 Add files via upload
    Première version du résumé du règlement de la compétition pour notre PAMI.
2025-11-03 Add ultrasonic distance measurement with HC-SR04
    This file implements an ultrasonic distance measurement using the HC-SR04 sensor. It includes initialization of peripherals, GPIO, and UART for output.
2025-11-13 Add light sensor reading and status reporting
    Implement light sensor functionality to read sensor states and print system status.
2026-01-12 ajout des fichier kicad
    [tuto-B_Cu.gbr, tuto-B_Mask.gbr, tuto-B_Paste.gbr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]
2026-01-12 ajout datasheet pin
    [PAMI-PIN-Datasheet.xlsx]
2026-02-02 restructuration des fichiers
    [PAMI-PIN-Datasheet.xlsx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]
2026-02-02 ajout du premier fichier 3D
    [Etage 1 PAMI STL.STL]
2026-02-02 ajout du répertoire pour les datasheets
2026-02-02 ajout XL-320-dimension
    [Etage 1 PAMI STL.STL]
2026-02-02 G431KBT6 pin placement
2026-02-03 ajout de la liste des composant
    [PAMI-Composants-PCB.xlsx]
2026-02-05 renseignement des composant et leu référence
    [PAMI-Composants-PCB.xlsx]
2026-02-09 ajout de la datasheet du régu 5V
2026-02-16 update pcb
    [PAMI_TEAM_SCRAT_FINAL.kicad_pcb, PAMI_TEAM_SCRAT_FINAL.kicad_sch]
2026-02-19 pcb termine
    [PAMI_TEAM_SCRAT_FINAL.kicad_pcb, PAMI_TEAM_SCRAT_FINAL.kicad_sch, mcu_stm32.kicad_sch]
2026-03-09 actualisation liste composants
    [PAMI-Composants-PCB.xlsx, PAMI-Composants-PCB2.xlsx]
2026-03-09 copy line follower project
    [Led_Phototransistor_package.kicad_sch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]
2026-04-17 Nouvelle version de la carte avec les corrections
    [PAMI_TEAM_SCRAT_FINAL_V2.csv, PAMI_TEAM_SCRAT_FINAL_V2.kicad_pcb, PAMI_TEAM_SCRAT_FINAL_V2.kicad_sch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]
2026-04-17 nouveau fichier gerber
    [PAMI_TEAM_SCRAT_FINAL_V2-B_Cu.gbl, PAMI_TEAM_SCRAT_FINAL_V2-B_Mask.gbs, PAMI_TEAM_SCRAT_FINAL_V2-B_Paste.gbp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]
2026-04-23 ajout code stlink fonctionnel
    [PAMI_TEAM_SCRAT_FINAL_V2.kicad_pcb]
2026-05-06 Correction de la liaison UART avec le STLINK
    [PAMI_TEAM_SCRAT_FINAL_V2.1.csv, PAMI_TEAM_SCRAT_FINAL_V2.1.kicad_pcb, PAMI_TEAM_SCRAT_FINAL_V2.1.kicad_sch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]

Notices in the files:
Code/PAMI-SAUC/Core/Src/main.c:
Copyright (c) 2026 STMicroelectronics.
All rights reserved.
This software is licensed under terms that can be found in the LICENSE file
